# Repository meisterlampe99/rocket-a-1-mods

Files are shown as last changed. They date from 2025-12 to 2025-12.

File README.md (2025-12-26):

## Fork from Alicja Musiał great Rocket model!

Implemented crude .stl fixes for known issues originally mentioned by Alicja.
- Launch lug now on bottom part, and removed from short and original body parts.
- Hook added to nose cone.

Also made these modifications
- increased the thread strength of the bottom part 
- a shorter center core to conserve weight for flying weak A6-4 motors.
  (With the these motors it will just work. Flies 35m and opens half way down just in time)

New files:
- `rocket_A-1_short.ork`: simulation model for shorter verion, please adapt your weights!
- `3D_printable_components\Body_short.stl`: shorter version of center core

To conserve weight I printed it with a single perimeter and 10% infill, and reduced the infill anchor lenght to a quarter.
I used 5mm brims on the bottom part to keep it attached to the print bed. Printed on Bambulab X1Carbon and Anycubic Vyper.
If holes at deretraction points of the outer perimeter appear, try minimal amounts of "extra lenght on deretraction" (e.g. 0.04mm)

If the recovery wadding is properly reinstalled after the first flight, the center core will survive a couple of starts.

Will try to print it in LW-PLA at some point in time.

Copyright 2021 @alicjamusial. 

- This work is licensed under a Creative Commons Attribution-ShareAlike 4.0 International License. 
- http://creativecommons.org/licenses/by-sa/4.0/ 
- Attribution-ShareAlike 4.0 International 
- Website from Alicja: https://alicja.space/projects/rocket-a-1/

Render of assembled short version rocket with original body next to it:
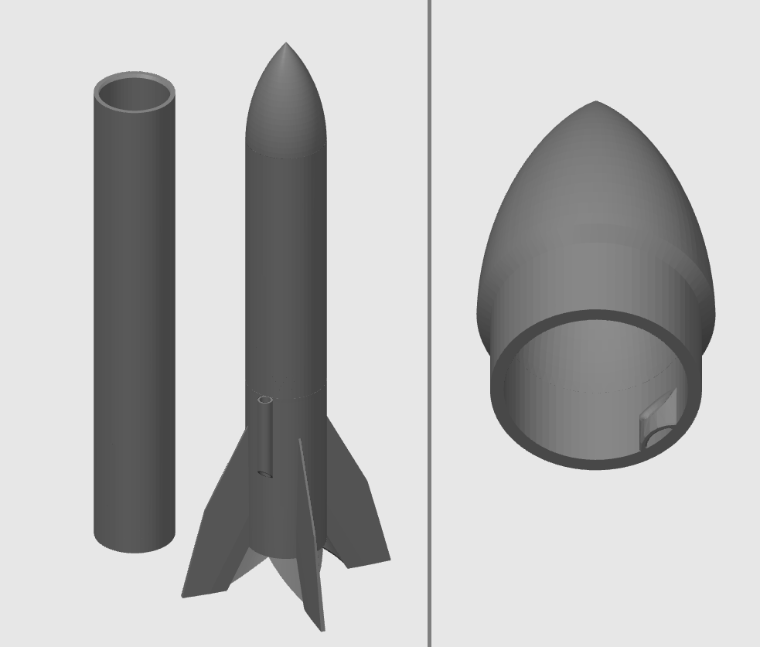
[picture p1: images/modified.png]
schema


Original description by Alicja:
# Rocket A-1 - 3D printed flying model rocket

schema

### ◾ About the project

**A-1** is a fully 3D-printable flying model rocket. It is threaded, so it doesn't require any glue to be assembled (except a little drop to attach the parachute or streamer cord to the cone (but I'll probably add a hook in the cone in incoming version to avoid this inconvenience)).

It is compatible with **Klima motors** (18mm diameter and 70mm length). It was tested with Klima C6-7 motor and flew nicely - the same model is ready to fly one more time.

Feel free to modify the model and create your own version best suited for your motor :). I'd love to see more A-1 fly!

schema

### ◾ Files
This project consists of:
- `rocket_A-1.ork` file - rocket model and simulation created with [Open Rocket](http://openrocket.info/) software
- `Rocket A-1.f3d` file - rocket 3D printable model created in Autodesk Fusion 360
- `3D_printable_components` folder with three parts in `*.stl` format, ready to be printed

schema

### ◾ How high will it fly?
- Simulation from the OpenRocket (included below) shows something about 220m. I didn't put the altimeter inside **yet**, but I guess it could have been something around it.

schema

- So just give it a try...
- ...or see how it takes off in action:

<p align="center">
  
</p>

### ◾ 3D printer hints
1. I printed the rocket on Ender 5 Pro. There's a possibility that your printer will require some adjustments in `*.stl` files to be able to print them properly.
2. It's good to use quite a big brims while printing fins - unfortunately they are quite likely to collapse and create not-so-nice PLA spaghetti 😬
3. I used PLA to print it, but ABS should be fine too. The rocket survived its first flight and it's getting ready for the next one, so PLA seems to be tough enough :).

schema

### ◾ Known issues
1. The nose cone lacks a hook to attach the cord from the parachute or streamer, so it's unavoidable to use a bit of glue.
2. Launch lug should be placed on the bottom component, between two fins (not on the middle component).

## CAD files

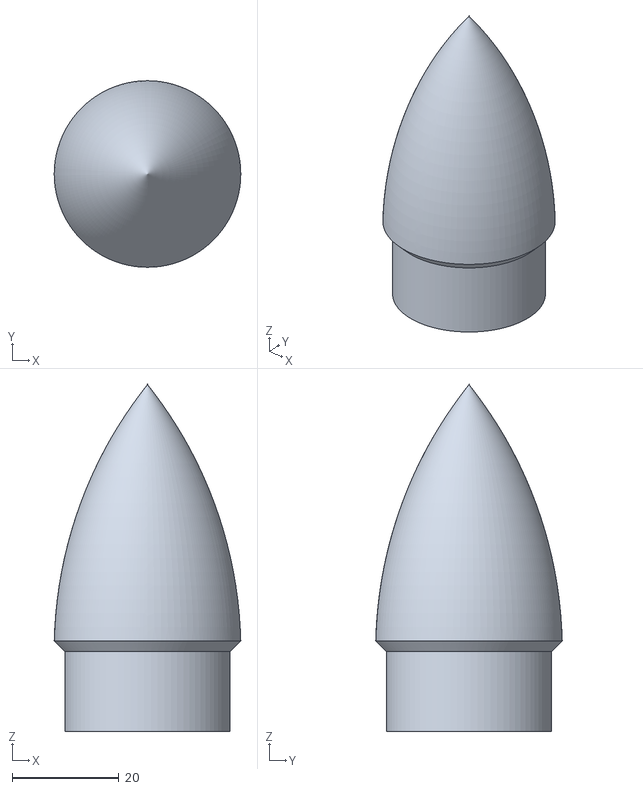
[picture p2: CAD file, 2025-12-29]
3D_printable_components/Head.stl
34.9 x 34.9 x 65.0

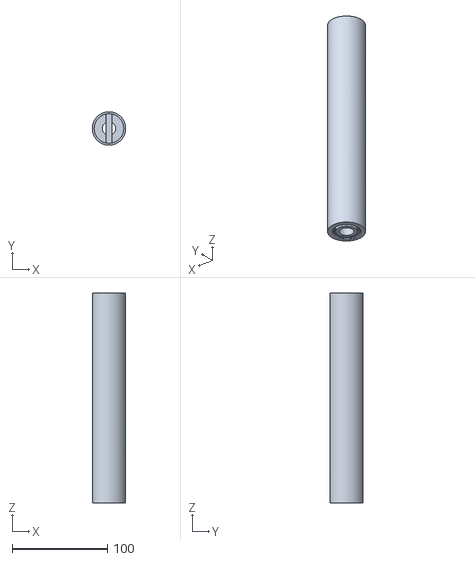
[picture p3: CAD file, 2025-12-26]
3D_printable_components/Body.stl
35.0 x 35.0 x 220.0

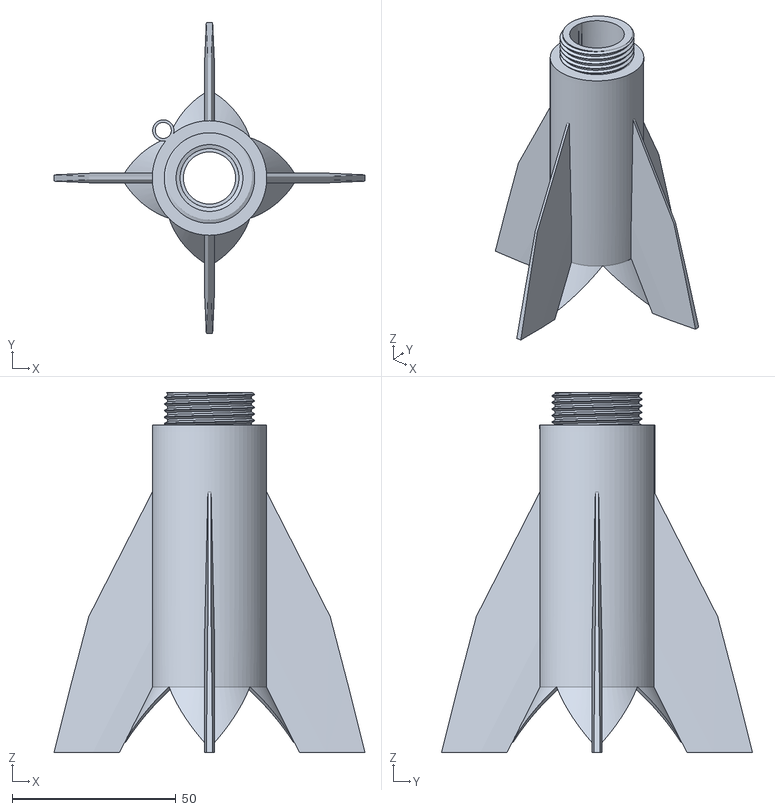
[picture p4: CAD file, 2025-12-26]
3D_printable_components/Bottom_And_Fins.stl
95.0 x 95.0 x 110.0

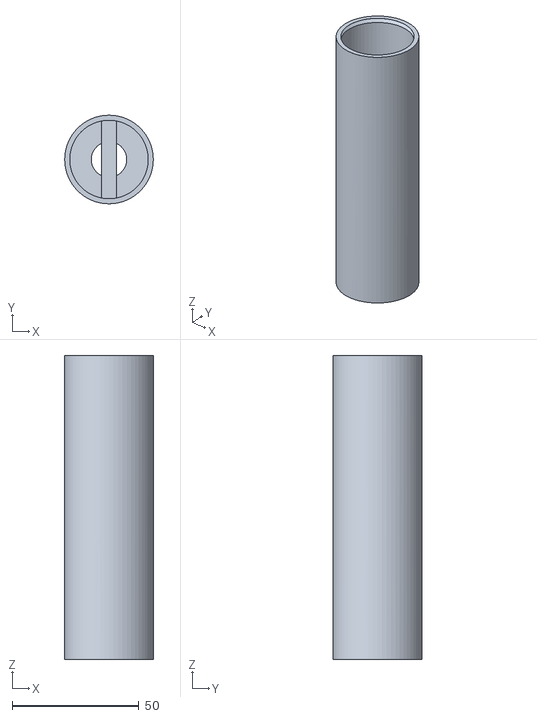
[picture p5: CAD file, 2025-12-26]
3D_printable_components/Body_short.stl
35.0 x 35.0 x 120.0

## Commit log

2025-02-04 short body for small motors
    Added a shortend version of the Body for flying with A6-4 motors.
    [Body_short.stl]
2025-02-04 increased thread strength on bottom part
    increased material thickness where the bottom thred is cut. Had to remove the top cavity.
    optionally an upside down cone with an axial hole could be added to preserve the top cavity and still increase thread strength but i went for a simple cylinder here.
    [Bottom_And_Fins.stl]
2025-02-04 added my print infos
2025-12-26 fixed known issues mentioned by alicja
    [Body.stl, Body_short.stl, Bottom_And_Fins.stl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]
2025-12-29 increased size of hook inside of nose cone for wider threads
    [Head.stl]
